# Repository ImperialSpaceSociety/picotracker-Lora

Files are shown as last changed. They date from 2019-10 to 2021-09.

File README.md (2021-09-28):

# Pico Ballon Tracker using LoRaWAN

## Objectives
This Pico balloon tracker is a new version to be designed by Imperial College Space Society. It is intended to offer an easy to build and low cost entry for people who want to launch small Helium filled balloons with a small tracking payload while using the Things Network LoRaWAN Network to receive the telemetry data from the balloon.

 implentation objective is to fly a small balloon around the world and to track it using the Things Network and HabHub.

## Major components
We have settled on the following components to go on the tracker solution. 

### Tracker

* Murata ABZ LoRa Module MCU with 868MHz LoRaWAN Radio and 32 Bit ARM CPU
* Ublox Max M8Q GPS module
* MS8607 Pressure temp humidity sensor
* Solar Power Management
* Possible small Energy storage by battery or super capacitor
The moto: KEEP IT SIMPLE

### TTN2HabHub Bridge

* Subscribe to Things Network Application for data from trackers
* Store Tracker data and meta data showing gateway information
* Forward tracking data to HabHub
* Possibly send data back to tracker
The bridge can be found in a seperate repo: [link](https://github.com/ImperialSpaceSociety/ttnhabbridge)

### Launch Gateway

* Portable Things Network LoRaWAN Gateway
* Cellular Internet Access to Things Network
* GPS
* Local Gateway Status Display
* Local Payload Data display

### Balloon

* Low cost 36 inch super pressure balloon
* Prestressed
* Helium Filled

### Tracker Firmware
All firmware used in the trackers can be found here: https://github.com/ImperialSpaceSociety/LoRaMac-node. Its a fork of the Semtech Loramac-node reference firmware.
Note that the code in the current repo is no longer used and is used for reference only.

# Flights
* ICSPACE15: [Flight report](https://www.union.ic.ac.uk/guilds/icseds/2020/01/long-range-lora-balloon-tracker-launch-from-london/)
* ICSPACE16: [Flight report](https://www.union.ic.ac.uk/guilds/icseds/2020/02/balloon-flights-to-austria-and-slovakia/)
* ICSPACE17: [Flight report](https://www.union.ic.ac.uk/guilds/icseds/2020/02/balloon-flights-to-austria-and-slovakia/)
* ICSPACE18: Was lost after launch
* ICSPACE19: [Flight report](https://www.union.ic.ac.uk/guilds/icseds/2020/03/launch-of-icspace19/)
* ICSPACE20 & 21: [Flight report](https://www.union.ic.ac.uk/guilds/icseds/2020/10/icspace21-flight-to-japan-and-icspace20/)
* ICSPACE22: [Flight report](https://www.union.ic.ac.uk/guilds/icseds/2020/12/first-unconfirmed-circumnavigation-of-the-earth-by-ic-space-society-balloon-icspace22/)
* ICSPACE23: [Flight report](https://www.union.ic.ac.uk/guilds/icseds/2020/12/icspace23-launch/)

Past flight paths may be viewed on the [map](https://charts.mongodb.com/charts-project-0-wlibw/public/dashboards/487e7641-c649-4822-abc5-f70eb2e155c7).

# Design Files
The PCBs are designed with Kicad and the latest designs can be found in the [hardware folder](hardware/Kicad/). We have two designs, the a and the b variant. a variant is a fully solar powered tracker with no power storage. The solar cells are directly wired to VCC and GND to power all components. b variant has a 50mAh lipo on board for power storage. The MPPT IC on board, the SPV1040, extracts maximum current from the cells to charge the battery.

As of 29/12/2020, the latest flight proven design is V1.3a. The b variant has not been flown yet.

The schematic of v1.3a is here:


Assembled tracker:

PCB top layer(v1.3a): 


PCB bottom layer(v1.3a):


# Software
We use the KEIL IDE to program the tracker. KEIL can be downloaded and used free of charge for the STM32L0 series of microcontrollers. You will be able to download Keil from [here](https://www2.keil.com/stmicroelectronics-stm32/mdk). Make sure you activate the licence so that you can compile files greater than 30kb of flash. There is no cost for the licence.

We use the ST link to program the STM32L0 microncontroller. You will likely need the ST-link Driver, which can be downloaded from their website: [link]( https://www.st.com/en/development-tools/stsw-link009.html#get-software)

To get the picotracker firmware, run the following to clone the repo. Useful tip: Ensure the repo is cloned to the root folder e.g. `C:\` because there have been issues with the path lengths of the files getting too long for Windows to handle. The repo has very very long paths, a legacy of the LoRaWAN firmware stack by STMicroelectronics.
```bash
git clone https://github.com/ImperialSpaceSociety/picotracker-Lora.git
```
The software on the latest tracker can be found in the [Software folder](Software). You need to navigate to ``Software/Projects/B-L072Z-LRWAN1/Applications/LoRa/End_Node/MDK-ARM/`` and you can open the KEIL project by clicking ``Lora.uvprojx``

Once you open Keil, it should look like this. Ensure that the 1.3a_variant of the code is selected(highlighted in picture): 

You will have to tell Keil that you are using the ST-link programmer. To do that, go to the `flash` drop down menu and select `Configure Flash Tools`. Then switch to the `debug` tab and ensure the drop down menu is set to `St-Link Debugger` as shown in the picture below. Then click the `settings` button.


When you open up the settings menu, it should look like this: 


Now that your st-link debugger is setup, its time to compile and program. Ensure the ST-link programmer is connected to the tracker, and hit compile and then upload or debug. Note: Its necessary to compile before uploading, or it will not have the latest hex file to flash to the tracker.


# Software overview
The picotracker state machine is as follows: 
It gets a GPS fix every 2 minutes and transmits it to ground



### Edits done over the reference version by STMicroelectronics
* Switching LoRaMAC regional settings depending on where it is
* Reduce tx power over US915/AU915
* Prevent sending empty frame after boot
* Use subband of 8 channels for US915/AU915
* Seperate credentials for each region of the world. 
* Prevent sticky uplinks after receiving channel change requests. Actually prevent any uplinks to test channel change requests. Wait till the next scheduled uplink.
* Different datarate for each region
* Polling specific date ranges for eeprom records
* 
# Photos
These are photos of ICSPACE19 before launch, during testing in the sun. It is a 1.1a variant, with no power storage.

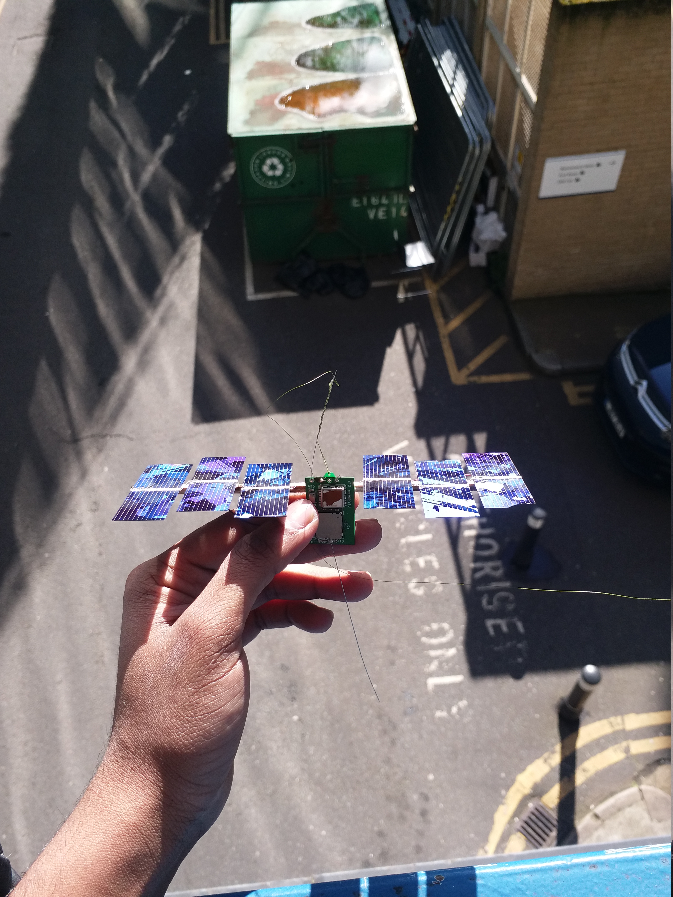
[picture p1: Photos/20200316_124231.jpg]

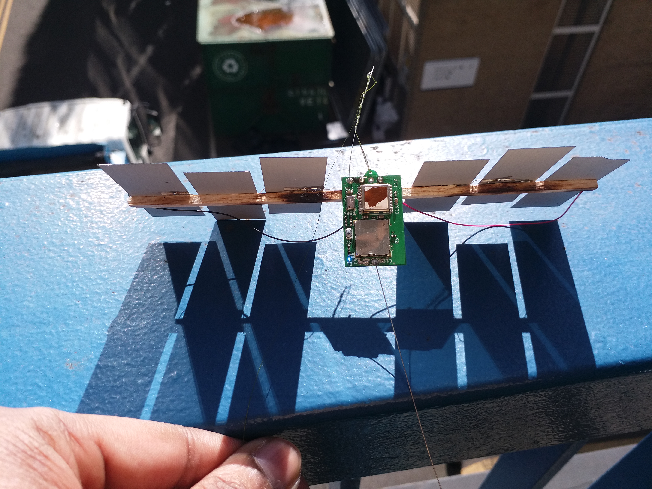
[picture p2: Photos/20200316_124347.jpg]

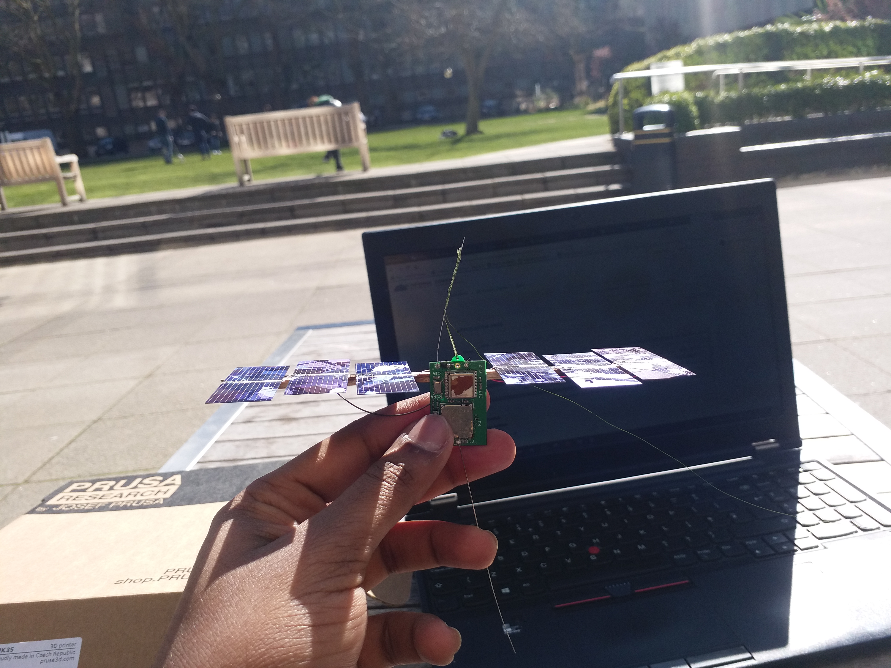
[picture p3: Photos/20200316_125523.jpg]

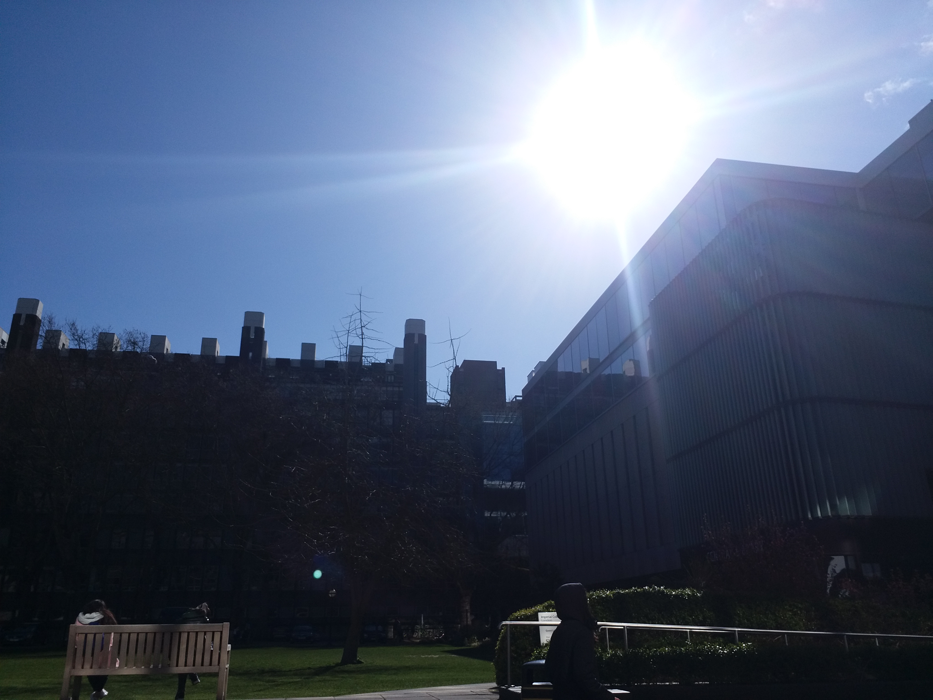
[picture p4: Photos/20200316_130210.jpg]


# Instructions for special tests of multiregion Lorawan

In this test, I want to test if the tracker will work properly over US915. We have had issues where some packets over Canada contained no payload data. I don't know the root cause. Could be power supply issues. To narrow down causes, I have created this test, to be run on the B-L072Z-LRWAN1.

This test will:
1. transmit every 2 minutes
2. a packet the size of our typical message
3. on US915 frequencies.

I want to find out if we receive any empty packets.

## How to run the program

Clone this project and switch to branch `multi-region-tests`. All tests on multi region lorawan will be here.
Navigate to `picotracker-Lora/Software/Projects/B-L072Z-LRWAN1/Applications/LoRa/End_Node/MDK-ARM/` and run `Lora.uvprojx` with Keil.

After opening the Keil project, switch the firmware config to work on the B-L072Z-LRWAN1 dev board. This can be done as follows: 

Now compile and upload the code into the dev board.

The board will output debug information at `20000000` baud. I normally use the Arduino editor's inbuilt terminal. 

An expected output on the terminal will look like this. It will initialise, and transmit a packet every 2 minutes. This packet will be the same size as the ones transmitted over Canada on ICSPACE22 and will be transmitting on US915 freqencies. This will replicate the same parameters of ICSPACE22 over Canada, where we saw that some packets did not contain any data at all. Note that this program will not need any peripherals(GPS, sensors etc).
```

************************************ 
* Picotracker Lora                 * 
* Imperial College Space Society   * 
************************************ 

SELFTEST: Initialising Hardware
SELFTEST: LED should blink now
SELFTEST: Now initing sensors
SELFTEST: Initialisng ms5607
SELFTEST: Now the radio should transmit
APP DUTY CYCLE(TX INTERVAL maybe longer depending on message length and datarate) : 12000
ABP
DevEui= 00-AB-DF-8A-62-F5-C1-81
DevAdd=  26011673
NwkSKey= D1 21 88 24 49 F6 0C 62 C0 C1 EF 4E FC 24 EC E4
AppSKey= 8F 3C F3 ED 51 FE 03 64 EC 0E 1A 06 6D 41 FC 9D

READING SENSOR AND GPS
================================================================
SENSOR AND GPS VALUES
================================================================
Temperature degrees C: 0.000000
Pressure mBar: 0.000000
Longitude: 0.000000 Latitude: 0.000000 altitude: 0
Solar voltage no load: 3
Solar voltage with GPS load: 0
================================================================
TX on freq 904600000 Hz at DR 4
⸮  1s615ms: PHY txDone
⸮RX on freq 923900000 Hz at DR 13
⸮  2s646ms: PHY rxTimeOut
⸮RX on freq 923300000 Hz at DR 8
⸮  3s698ms: PHY rxTimeOut
  3s707ms: APP> McpsConfirm STATUS: OK

  3s707ms: #= U/L FRAME 6640 =# Class A, Port 99, data size 26, pwr 2, Channel Mask FF00 

⸮READING SENSOR AND GPS

================================================================
SENSOR AND GPS VALUES
================================================================
Temperature degrees C: 0.000000
Pressure mBar: 0.000000
Longitude: 0.000000 Latitude: 0.000000 altitude: 0
Solar voltage no load: 3
Solar voltage with GPS load: 0
================================================================
TX on freq 904600000 Hz at DR 4
⸮ 13s642ms: PHY txDone
⸮RX on freq 923900000 Hz at DR 13
⸮ 14s673ms: PHY rxTimeOut
⸮RX on freq 923300000 Hz at DR 8
⸮ 15s726ms: PHY rxTimeOut
 15s735ms: APP> McpsConfirm STATUS: OK

 15s735ms: #= U/L FRAME 6641 =# Class A, Port 99, data size 26, pwr 2, Channel Mask FF00 
```
### Speed up debugging tips
If you want to speed up the process for debugging, in `main.h`, you can set `APP_TX_DUTYCYCLE` to a lower value to increase the frequency of transmissions.
```c
#define APP_TX_DUTYCYCLE                           120000
```

For debugging, you can switch the end node to transmit on EU868 frequencies by making the following changes to `geofence.c`
```c
LoRaMacRegion_t current_loramac_region = LORAMAC_REGION_EU868;  // Loramac region EU868
Polygon_t curr_poly_region = EU863870_EUROPE_polygon; // Europe is in this polygon
```

### Verify the data(the actual test)
Now if everything is working on the end node side, it is time to see what is appearing on the TTN console. 
You should be able to see packets of data that look something like this. The important thing is, in order to pass this test, every packet should have a `payload_raw` and `payload_fields` section. During ICSPACE22's flight over Canada, we found that some packets did not contain the `payload_fields` section. I want to find out if it is a software issue that causes it.

Note, that every single piece of MQTT data is archived [here](http://medadnewman.co.uk/wp-content/uploads/2020/10/mqtt_log_data-1.txt) for reference. 
```json
{
  "app_id": "icss_lora_tracker",
  "dev_id": "icspace23",
  "hardware_serial": "0093BECA9134091B",
  "port": 99,
  "counter": 6603,
  "payload_raw": "AHN2YwFnERICiAAAAAAAAAAAAAMCAAAEAQA=",
  "payload_fields": {
    "analog_in_3": 0,
    "barometric_pressure_0": 3030.7,
    "digital_out_4": 0,
    "gps_2": {
      "altitude": 0,
      "latitude": 0,
      "longitude": 0
    },
    "temperature_1": 437
  },
  "metadata": {
    "time": "2020-11-06T22:20:03.034197954Z",
    "frequency": 868.5,
    "modulation": "LORA",
    "data_rate": "SF8BW125",
    "airtime": 154112000,
    "coding_rate": "4/5",
    "gateways": [
      {
        "gtw_id": "eui-58a0cbfffe800f4d",
        "timestamp": 3440028508,
        "time": "2020-11-06T22:20:03.082736968Z",
        "channel": 0,
        "rssi": -67,
        "snr": 8.5,
        "rf_chain": 0
      }
    ]
  }
}

```

## License

Hardware is Licensed under CERN OHL v.1.2 or later https://www.ohwr.org/documents/294 No warranty is provided for this documentation implied or otherwise.

Software is licensed under MIT License.

MIT License

Copyright (c) 2018 Imperial College Space Society

Derived Software  Copyright (c) 2014  Richard Meadows <richardeoin>

Permission is hereby granted, free of charge, to any person obtaining a copy of this software and associated documentation files (the "Software"), to deal in the Software without restriction, including without limitation the rights to use, copy, modify, merge, publish, distribute, sublicense, and/or sell copies of the Software, and to permit persons to whom the Software is furnished to do so, subject to the following conditions:

The above copyright notice and this permission notice shall be included in all copies or substantial portions of the Software.

THE SOFTWARE IS PROVIDED "AS IS", WITHOUT WARRANTY OF ANY KIND, EXPRESS OR IMPLIED, INCLUDING BUT NOT LIMITED TO THE WARRANTIES OF MERCHANTABILITY, FITNESS FOR A PARTICULAR PURPOSE AND NONINFRINGEMENT. IN NO EVENT SHALL THE AUTHORS OR COPYRIGHT HOLDERS BE LIABLE FOR ANY CLAIM, DAMAGES OR OTHER LIABILITY, WHETHER IN AN ACTION OF CONTRACT, TORT OR OTHERWISE, ARISING FROM, OUT OF OR IN CONNECTION WITH THE SOFTWARE OR THE USE OR OTHER DEALINGS IN THE SOFTWARE.

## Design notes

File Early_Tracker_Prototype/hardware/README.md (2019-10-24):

## TODO
* set up circuit to measure solar voltage
* verify if gps circuit is correct
* layout the PCB

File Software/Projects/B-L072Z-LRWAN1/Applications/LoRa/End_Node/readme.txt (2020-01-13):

/**
  @page End_Node Readme file
 
  @verbatim
  ******************************************************************************
  * @file    End_Node/readme.txt 
  * @author  MCD Application Team
  * @brief   This application is a simple demo of a LoRa Object connecting to 
  *          a LoRa Network. 
  ******************************************************************************
  *
  * Copyright (c) 2018 STMicroelectronics. All rights reserved.
  *
  * This software component is licensed by ST under Ultimate Liberty license
  * SLA0044, the "License"; You may not use this file except in compliance with
  * the License. You may obtain a copy of the License at:
  *                               www.st.com/SLA0044
  *
  ******************************************************************************
   @endverbatim

@par Example Description

This directory contains a set of source files that implements a simple demo of an end 
device also known as a LoRa Object connecting to a Lora Network. The LoRa Object can be 
   - either a STM32LXxx-Nucleo board and Lora Radio expansion board, optionnally a sensor board. 
   - or a B-L072Z-LRWAN1 (available soon)
By setting the LoRa Ids in comissioning.h file according to the LoRa Network requirements, 
the end device will send periodically the sensor data to the LoRa network.
  ******************************************************************************

@par Directory contents 

  - End_Node/LoRaWAN/App/inc/bsp.h               Header for bsp.c
  - End_Node/LoRaWAN/App/inc/Commissioning.h     End device commissioning parameters
  - End_Node/LoRaWAN/App/inc/debug.h             interface to debug functionally
  - End_Node/LoRaWAN/App/inc/hw.h                group all hw interface
  - End_Node/LoRaWAN/App/inc/hw_conf.h           file to manage Cube SW family used and debug switch
  - End_Node/LoRaWAN/App/inc/hw_gpio.h           Header for hw_gpio.c
  - End_Node/LoRaWAN/App/inc/hw_msp.h               Header for driver hw msp module
  - End_Node/LoRaWAN/App/inc/hw_rtc.h            Header for hw_rtc.c
  - End_Node/LoRaWAN/App/inc/hw_spi.h            Header for hw_spi.c
  - End_Node/LoRaWAN/App/inc/utilities_conf.h    configuration for utilities
  - End_Node/LoRaWAN/App/inc/vcom.h              interface to vcom.c
  - End_Node/LoRaWAN/App/inc/version.h           version file
  - End_Node/Core/inc/stm32lXxx_hal_conf.h       Library Configuration file
  - End_Node/Core/inc/stm32lXxx_hw_conf.h        Header for stm32lXxx_hw_conf.c
  - End_Node/Core/inc/stm32lXxx_it.h             Header for stm32lXxx_it.c
  
  - End_Node/LoRaWAN/App/src/bsp.c               manages the sensors on the application
  - End_Node/LoRaWAN/App/src/debug.c             debug driver
  - End_Node/LoRaWAN/App/src/hw_gpio.c           gpio driver
  - End_Node/LoRaWAN/App/src/hw_rtc.c            rtc driver
  - End_Node/LoRaWAN/App/src/hw_spi.c            spi driver
  - End_Node/LoRaWAN/App/src/main.c              Main program file
  - End_Node/LoRaWAN/App/src/vcom.c              virtual com port interface on Terminal
  - End_Node/Core/src/stm32lXxx_hal_msp.c        stm32lXxx specific hardware HAL code
  - End_Node/Core/src/stm32lXxx_hw.c             stm32lXxx specific hardware driver code
  - End_Node/Core/src/stm32lXxx_it.c             stm32lXxx Interrupt handlers
 
@par Hardware and Software environment 

  - This example runs on STM32L053R8, STM32L073RZ, STM32L152RE and STM32L476RG devices.
    
  - This application has been tested with STMicroelectronics:
    NUCLEO-L053R8 RevC
    NUCLEO-L073RZ RevC
    NUCLEO-L152RE RevC
    NUCLEO-L476RG RevC	
    B-L072Z-LRWAN1 RevC
    boards and can be easily tailored to any other supported device 
    and development board.

  - STM32LXxx-Nucleo Set-up    
    - Connect the Nucleo board to your PC with a USB cable type A to mini-B 
      to ST-LINK connector (CN1 / CN7 on B-L072Z-LRWAN1).
    - Please ensure that the ST-LINK connector CN2 (CN8 on B-L072Z-LRWAN1) jumpers are fitted.
  -Set Up:

             --------------------------  V    V  --------------------------
             |      LoRa Object       |  |    |  |      LoRa Netork       |
             |                        |  |    |  |                        |
   ComPort<--|                        |--|    |--|                        |-->Web Server
             |                        |          |                        |
             --------------------------          --------------------------

@par How to use it ? 
In order to make the program work, you must do the following :
  - Open your preferred toolchain 
  - Rebuild all files and load your image into target memory
  - Run the example
  - Open two Terminals, each connected the respective LoRa Object
  - Terminal Config = 115200, 8b, 1 stopbit, no parity, no flow control ( in src/vcom.c)
   
 * <h3><center>&copy; COPYRIGHT STMicroelectronics</center></h3>
 */

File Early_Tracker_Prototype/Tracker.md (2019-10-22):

# Tracker Prototype

It was decided to prototype key features of the new tracker on develop board before starting detail of hardware and firmware design.

### Tracker

* Murata ABZ LoRa Module MCU with 868MHz LoRaWAN Radio and 32 Bit ARM CPU
* Ublox Max M8Q GPS module
* MS8607 Pressure temp humidity sensor
* Solar Power Management
* Peripheral Power Control to minimise power consumption
* Possible small Energy storage by battery or super capacitor
* Reset Manager to ensure no corruption in case of brown outs
The moto: KEEP IT SIMPLE

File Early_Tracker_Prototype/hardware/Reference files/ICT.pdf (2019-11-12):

## ICT-series WSPR balloon tracker capable of WSPR and JT9

Rev. 1, September 2019

## Instructions

Original based on HABalloon by Stephen KD2NDR, Miami, Florida, October 25 2018

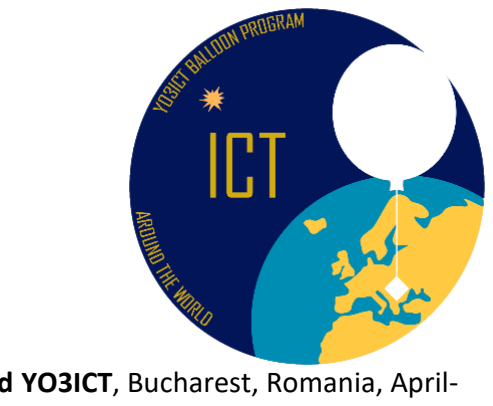
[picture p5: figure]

Improvements, advanced telemetry, new features, ground testing and flight testing by Eduard YO3ICT, Bucharest, Romania, April-September 2019

Credits also go to Hans G0ULP for developing the telemetry protocol and to David VE3KCL, Mike SA6BSS and Ben PE2BZ for all the help received during testing and flying.

You may use and modify the following code to suit your needs so long as it remains open source and it is for non-commercial use only.

The following software and hardware flew on ICT1, ICT2 and ICT3 balloons in 2019.

In the provided archive you will find the source code and the PCB layout files. This document is provided as a tutorial to get you up and running.
Fly at your own risk and follow your local aviation laws.

## Contact:

## Firmware instructions

All of the following assume that you are using the usbasp AVR programmer.

Before going into the firmware itself, our little board’s AVR chip runs at 4MHz. We need to set up some fuse bits using avrdude command lines.

We need to set the AVR to run on the external 4MHz resonator and the BOD level at 1.8V (Low fuse FD, High fuse DA, Extended fuse 06).

Avrdude commands:

avrdude -c usbasp -p m328p -v -U lfuse:w:0xFD:m

avrdude -c usbasp -p m328p -v -U hfuse:w:0xDA:m

avrdude -c usbasp -p m328p -v -U efuse:w:0x06:m

Install the latest Arduino IDE.

Then we set up our little board with the correct initialization.

Copy the code from the included boards.txt file to the end of your boards.txt file found under Program Files/arduino/hardware/arduino/avr and then choose this board in the Tools menu.

Next, we are using the delayMicroseconds function. We need to get the Arduino IDE aware of our 4Mhz clock. You'll need to replace the wiring.c file under Program Files/arduino/hardware/arduino/avr/cores/arduino. Replace the existing file with the one found in the archive.

Libraries required:

1. Time library : https://github.com/PaulStoffregen/Time
2. GPS library https://github.com/mikalhart/TinyGPSPlus
3. Si5351 library https://github.com/etherkit/Si5351Arduino
4. JT Encode library https://github.com/etherkit/JTEncode

Download all of them and install them in your libraries directory. You can also use Sketch – Include library menu from the Arduino IDE. Just point it to the zip file of each library and they will be installed quickly.

Edit the files to fit your conditions.

Important settings to do:

1. Callsign is set in the main .ino file on line 31. The provided source code comes with the fake callsign AA0AAA
2. Actual Si5351 oscillator frequency is set on line 242 of TelemFunctions.h. The provided source code comes with 27000000, meaning 27MHz
3. In ModeDef.h lines 11 and 12 we define the actual on-air frequencies for JT9 and WSPR
4. The telemetry channel is set in TelemFunctions.h on lines 80 and 81. Basically, we hard-code the first and the third characters of the telemetry callsign.

Please read this: http://www.qrp-labs.com/ultimate3/ve3kcl-balloons/ve3kcl-s4.html#protocol to get a better understanding of the telemetry protocol and channels.

Please read this: http://hojoham.blogspot.com/2016/10/known-flight-ids.html for known flight IDs. Ask Mike KD2EAT to get your channel assigned. Note: The list might change, as it contains some invalid channels (the ones starting with “1”).

The provided source code comes with an invalid telemetry channel to avoid interference while testing.

5. In TelemFunctions.h there are a lot of math functions (function loc_dbm_telem), including the temperature and solar voltage conversion formulas. Please calibrate them. Each AVR device may give different results. I provide a sample sketch (TEMP_VOLT_TEST). The PCB has a pad named TX. Hook up your UART to USB dongle to get the data out.
6. The source code provided has build-in three timing files for different timings of the WSPR and/or JT9 modes. The file can be selected within the main .ino file on line 61. You can include a different file. The only flight proven timing file is timing3.h. You can also domake your own file. Just test. And test again. And test once more before flight.

The timing3.h file uses both JT9 and WSPR. The transmission schedule is based on a 6 minute transmission cycle:

Minute 2 - JT9 - Callsign + 6-digit locator
Minute 3 - JT9 - 7th and 8th of the extended 8-digit locator + Altitude + Ground speed
Minute 4 - WSPR - Standard WSPR message
Minute 6 - WSPR - WSPR telemetry

Minute 12 - WSPR - Standard WSPR message
Minute 14 - WSPR - WSPR telemetry Minute 16 - WSPR - Standard WSPR message

Minute 22 - WSPR - Standard WSPR message Minute 24 - WSPR - WSPR telemetry Minute 26 - WSPR - Standard WSPR message

Minute 32 - JT9 - Callsign + 6-digit locator
Minute 33 - JT9 - 7th and 8th of the extended 8-digit locator + Altitude + Ground speed Minute 34 - WSPR - Standard WSPR message
Minute 36 - WSPR - WSPR telemetry

Minute 42 - WSPR - Standard WSPR message
Minute 44 - WSPR - WSPR telemetry Minute 46 - WSPR - Standard WSPR message

Minute 52 - WSPR - Standard WSPR message Minute 54 - WSPR - WSPR telemetry Minute 56 - WSPR - Standard WSPR message

Known bugs

Solar voltage is reported incorrectly. The hardware resistor divider R4 & R6 values should be changed to allow for greater voltage swing. The voltage formula must be recalculated as well.

## Hardware instructions

The PCB files provided are flight proven. Use a 50ohm resistor dummy load for testing. The PCB is 0.6mm thick.

Solder all the components. Note: The tracker won’t start without the GPS module.

The GPS antenna is made of 4.5cm of guitar string wire. It has a dedicated mounting hole.

The solar panels (6 pieces, the 39x19mm size) are soldered together in series using guitar string wire.

Pictures for reference:

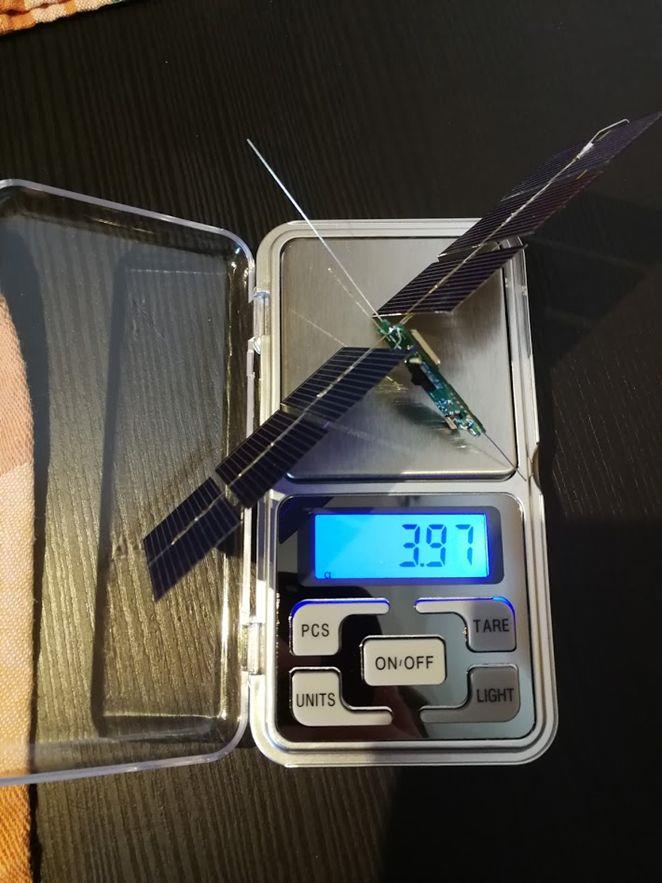
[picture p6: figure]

Three panels on each side.

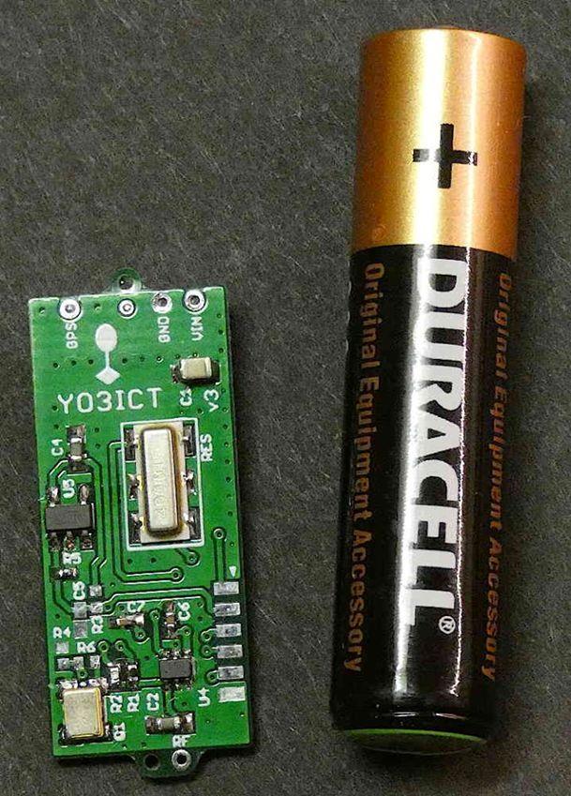
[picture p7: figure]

There are some holes on the PCB for power (which comes also via guitar string wire) and an isolated tinned hole near the top, just below the top tether hole.

That isolated tinned hole is for suspending the solar cells. The guitar string wire segment that connects the 3rd to the 4th solar cell is passing through that hole and is soldered. This provides stiffness as well as flexibility in the solar panel system. This is essential to ensure trouble-free mounting, handling, launching and flying.

The antenna is made of thin 0.1mm copper wire suspended by 0.08mm dynemaa fishing string. The string attaches to the two dummy holes at top and bottom of the PCB. The ’hot’ part of the dipole attaches to the dedicated hole named RF at the bottom. The ’cold’ part of the dipole gets attached to GND AFTER the solar panels have been attached. Try to provide some slack to the thin copper antenna wire before soldering. Failing to do so might result in broken solar cells or antenna wires.

Solar cells need to be soldered quickly and cleanly. Use flux, pre-solder the guitar string wire and use a temperature controller soldering iron (~330 degrees Celsius). Also, solar panels should be as horizontal as possible, otherwise the startup sun angle will be unpredictable.

The programming port pads are located on the side of the PCB and the white arrow points to the positive pad. The connector needed is a 1.27mm pitch row connector. This is to be removed before flight to save weight. Also clean the pads to get rid of excess solder. The programming layout is custom due to the PCB limitations.

In the end, the PCB is coated with some lacquer and then it is covered with kapton tape. This increases the thermal mass a bit, avoids moisture on the PCB and also helps with some basic thermal insulation.

The tracker and solar cells must came close to 4 grams weight and the antenna (whole dipole for 14MHz) should weigh less than one gram.

## What balloon to use?

SBS balloon or Chinese clear balloons, found on Aliexpress? As the SBS balloons are very expensive, we’ll discuss the cheap ones.

Order as many as you can afford. Usually, the ones from the center of the packaging are damage-free.

The balloons need to be pressure tested and pre-stretched to allow for greater internal volume and higher altitude. Your best shot at circumnavigation is to fly above 11000m, at least.

Required:

1. Air mattress pump for rapid inflation/deflation
2. Aquarium pump for controlled presurization
3. Digital, differential manometer

Basically, the pre-stretch process is a matter of time, pressure and temperature.

To shed weight, cut the excess material around the balloon edge and also cut the top tether, unless you do a dual launch. Do this BEFORE any attempt at balloon presurization.

Target differential pressure is above 0.6 psi. Go slowly above 0.4 psi. This will also highlight defective balloons. Use the hair dryer on moderate position to heat the balloon as you increase the pressure.

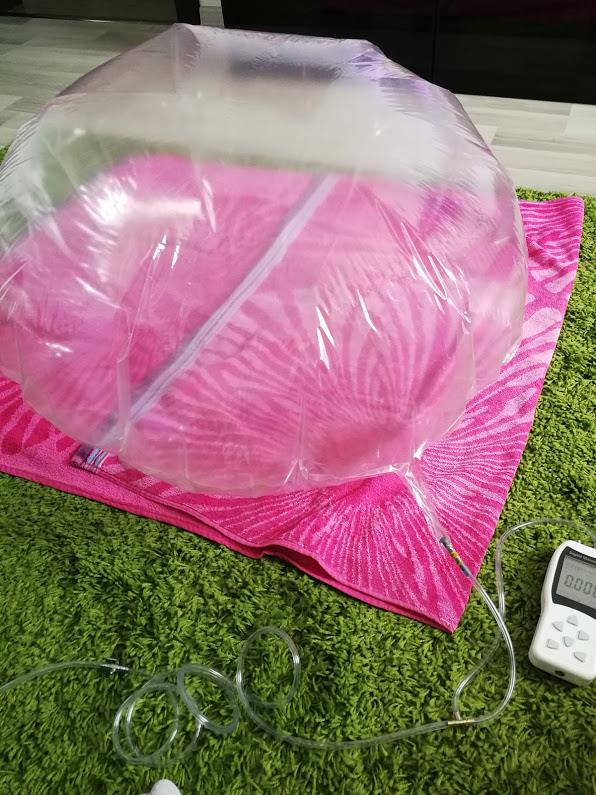
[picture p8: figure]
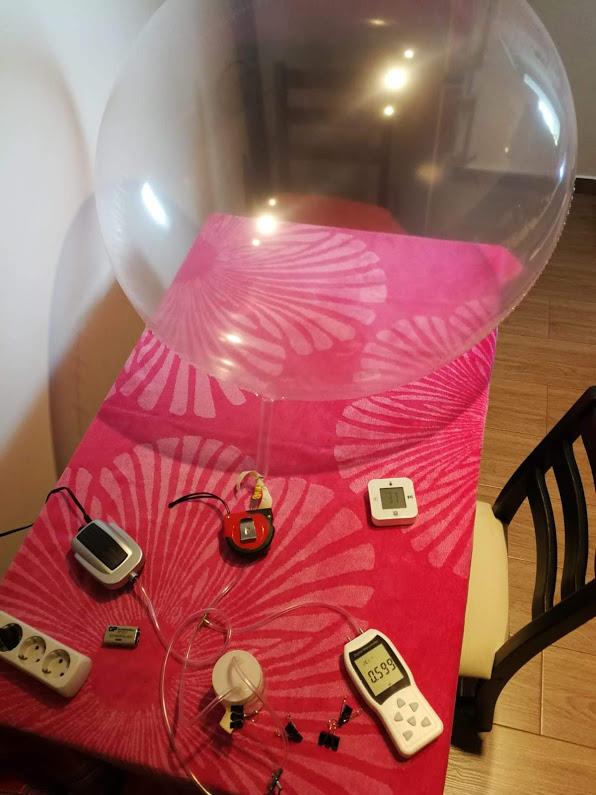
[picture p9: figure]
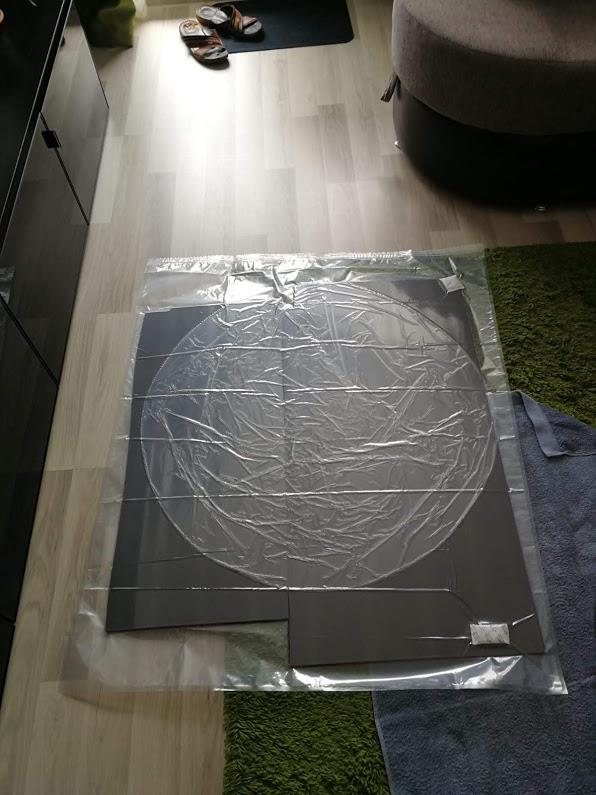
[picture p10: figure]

The target should be a pressure of around 0.6-0.65 psi, no balloon wrinkles on the edge and let it sit overnight. You will want to experiment as different balloons and different pressures and temperatures means different results. Not all balloons are created equal. David VE3KCL and Mike SA6BSS have a lot of experience with this type of balloon.

After the overnight pressurization, it is time to put the balloon to storage, in preparation for launch. Use a clothes vacuum bag and some dessicant bags. Avoid excess stress on the balloon!

## Launch

Use H2 for the best performance and highest altitude.

If using He, use the purest available, some retailers only offer 80% this will result in reduced performance and altitude.

1. Lay out a sheet to unfold the balloon on. Handle the balloon with care, try not to wrinkle the film any more than you have to. Avoid wearing clothes with zippers or buttons that may come in contact with the balloon.
2. Filling and launching a super pressure balloon requires a very special skill set. The most important is filling the balloon so it has the correct free lift. Please fill indoors and turn off heating and air conditioning, so the room is very still. Weigh everything that will be attached to the balloon, tracker, load line, tape, etc. Then add a maximum of 8 grams of free lift. I recommend you practice these procedures with a party balloon to refine your skills because if you over fill the balloon it will burst.
3. Once the fill is done, it’s time to seal the neck.
4. Set the iron to around 140 degrees Celsius. You can experiment with different temperatures here.
5. You need a hard surface like wood to put a piece of a mouse pad on. Make sure there are no sharp edges. Lay the balloon neck down on the mouse pad.
6. Use a piece of parchment paper. Cut a piece of it to lay on top of the neck so the iron does not come in direct contact with the film.
7. Press the edge of the iron down FIRMLY on top of the parchment paper and hold iron in place for 3 to 5 seconds.
8. Iron the rest of the neck.
9. Attach payload to the neck of the balloon. You can trim the neck at this point.
10. Time to launch – good luck! Avoid launching in the winter. Low sun angle means that the daily run time of the tracker will be very low. Avoid launching in high winds. Avoid launching near airports.

Sealed neck pictures:

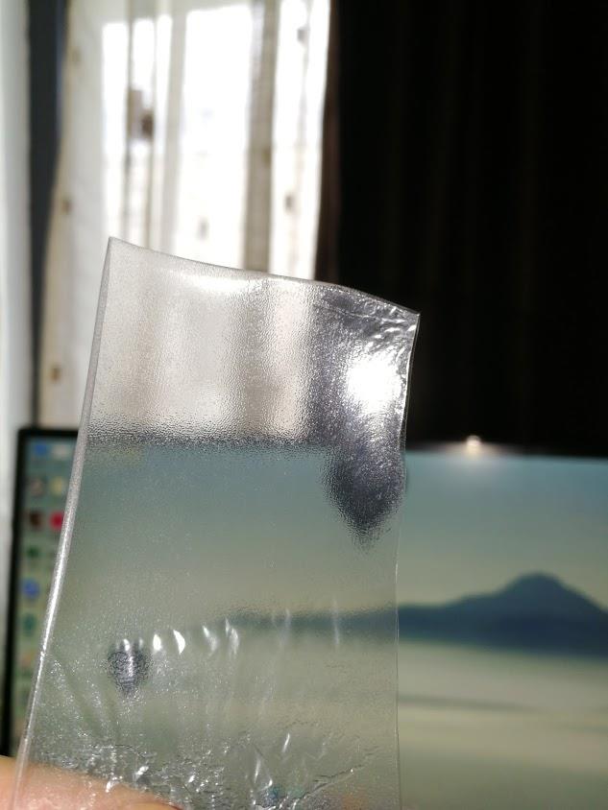
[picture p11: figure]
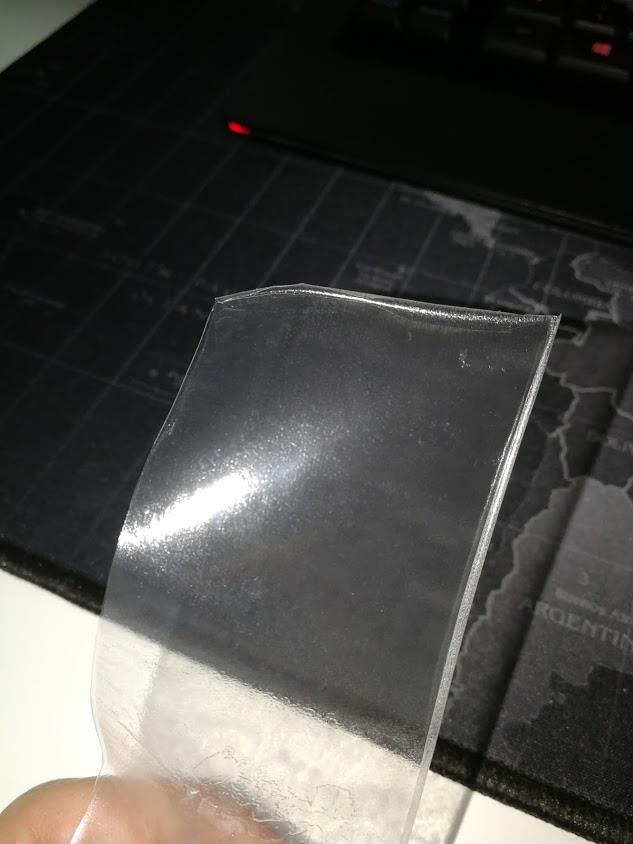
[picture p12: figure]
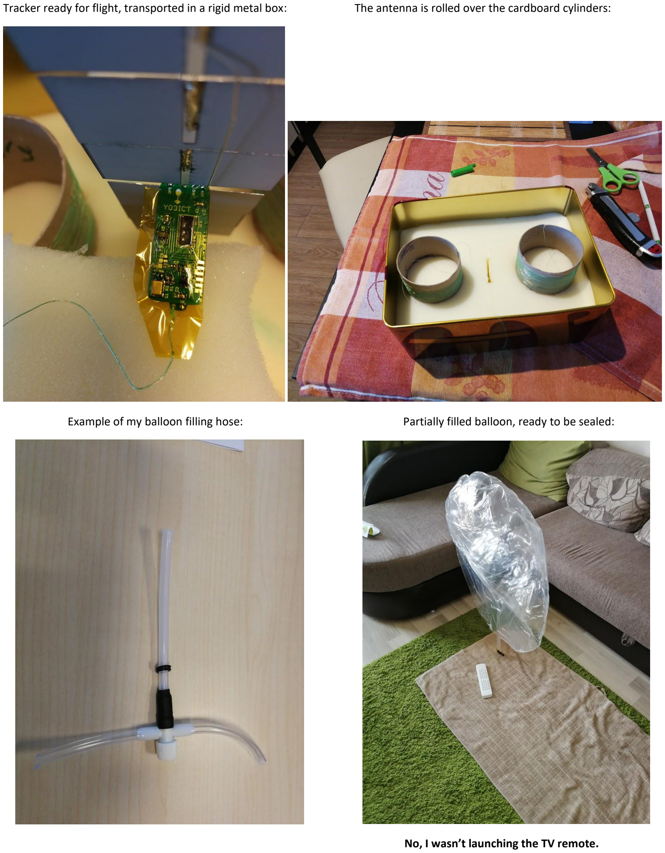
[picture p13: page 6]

Tracker ready for flight, transported in a rigid metal box: | The antenna is rolled over the cardboard cylinders:
Example of my balloon filling hose: | Partially filled balloon, ready to be sealed:

No, I wasn’t launching the TV remote.

ICT1 launch. You can clearly see the top and bottom antenna legs with the tracker in the middle:

## Tracking

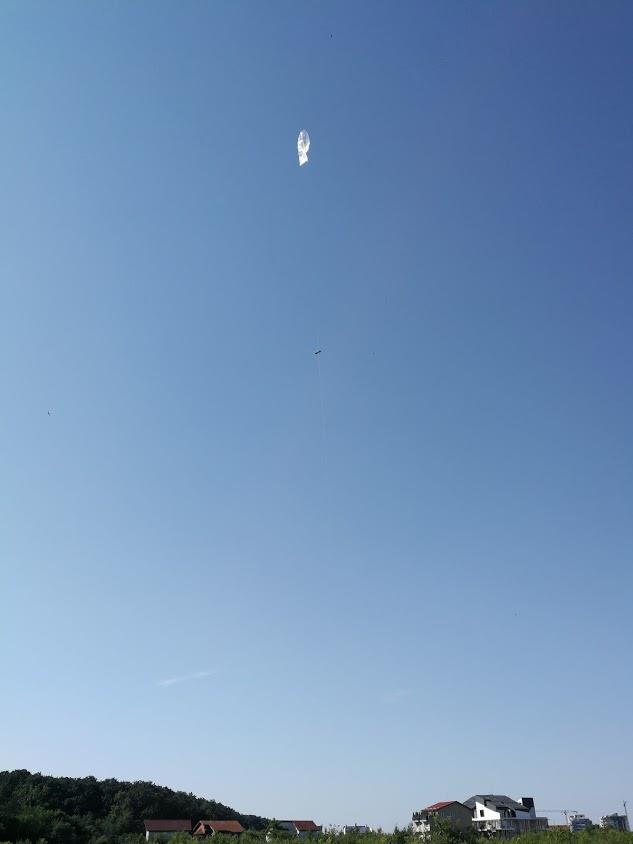
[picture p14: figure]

To get your balloon tracker on the tracker.habhub.org page please send email to David SM3ULC. You can also keep your own tracking map by programming a Phyton script or some VB code inside an Excel file. Contact me if you need help.

The WSPR network is big, but there’s an area with very low coverage : East-Central Asia. You’ll need to help your balloon by using some of the available KiwiSDRs (sdr.hu) from that area.

The best KiwiSDRs are Novosibirsk and Khabarovsk (Russia), Fukushima (Japan), Hawaii and KPH (California). Not all of them are always online. Do not rely on the build-in WSPR decoder. Feed the audio to a local instance of WSJT-X.

## Good luck and clear skies!

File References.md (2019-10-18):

# Links to Useful Documents

## SAM L21
[Datasheet and Reference manual](https://www.farnell.com/datasheets/2014285.pdf)

[Atmel� Software Framework (ASF) Reference Manual](http://ww1.microchip.com/downloads/en/AppNotes/Atmel-42699-ASF-Manual-(SAML21)_ApplicationNote_AT11513.pdf)

[Getting started guidelines](http://ww1.microchip.com/downloads/en/AppNotes/atmel-42410-getting-started-with-saml21_application%20note_at03975.pdf)

[SAM L21 Xplained Pro manual](http://ww1.microchip.com/downloads/en/devicedoc/atmel-42405-saml21-xplained-pro_user-guide.pdf)

## Si4468
[Datasheet](https://www.silabs.com/documents/public/data-sheets/Si4464-63-61-60.pdf)

[Programming Guide](https://www.silabs.com/documents/public/application-notes/AN633.pdf)

[API Documentation](http://www.silabs.com/documents/public/application-notes/EZRadioPRO_REVB1_API.zip)

## Bristol SEDS

[Main Page](http://www.bristol-seds.co.uk/)

[PicoTracker GitHub](https://github.com/bristol-seds/pico-tracker)

## HAB

[UKHAS Google Group](https://groups.google.com/forum/#!forum/ukhas%5B261-280%5D)

## uBlox

[BN-220](https://surehobby.com/desc/HR/HR5512/BN_220_GPS_Antenna_datasheet.pdf)

[UBX-M8030 Specification](https://www.u-blox.com/sites/default/files/products/documents/UBX-M8030-KT-FT_ProductSummary_%28UBX-14001605%29.pdf)

[Protocol Specification](https://www.u-blox.com/sites/default/files/products/documents/u-blox8-M8_ReceiverDescrProtSpec_%28UBX-13003221%29_Public.pdf)

## BME280

[BME280 Data Sheet](https://www.embeddedadventures.com/datasheets/BME280.pdf)

[Official Bosch C Driver](https://github.com/BoschSensortec/BME280_driver)

[Larry Banks C library](https://github.com/bitbank2/bme280)

## RFM98W

[Datasheet](http://www.farnell.com/datasheets/1870822.pdf)

[SX127x Datasheet](https://cdn-shop.adafruit.com/product-files/3179/sx1276_77_78_79.pdf)

[C Code example](https://github.com/wdomski/SX1278-example)

## UKHAS Lora

[Tracking Guide](https://ukhas.org.uk/guides:lora_tracking_guide)

## Stuart Robinsons Tracker

[Lora Tracker](http://www.loratracker.uk/?p=30)

[Github](https://github.com/LoRaTracker)

## TomasTT7 Trackers

[TT7B Tracker Blog](http://tt7hab.blogspot.com/2018/09/the-tt7b-tracker.html)

[tt7B Github](https://github.com/TomasTT7/TT7B-Tracker)

## Pi in the Sky

[Lora Tracker](http://www.pi-in-the-sky.com/index.php?id=making-a-lora-tracker)

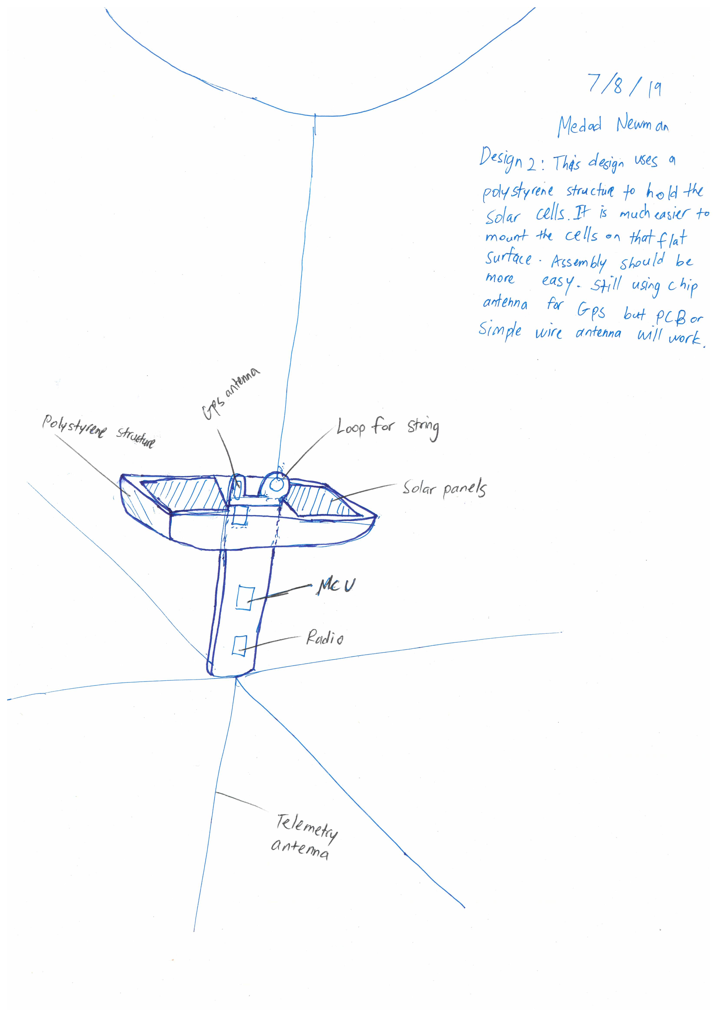
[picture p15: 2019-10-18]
Early_Tracker_Prototype/hardware/Plans/Design 2.jpg

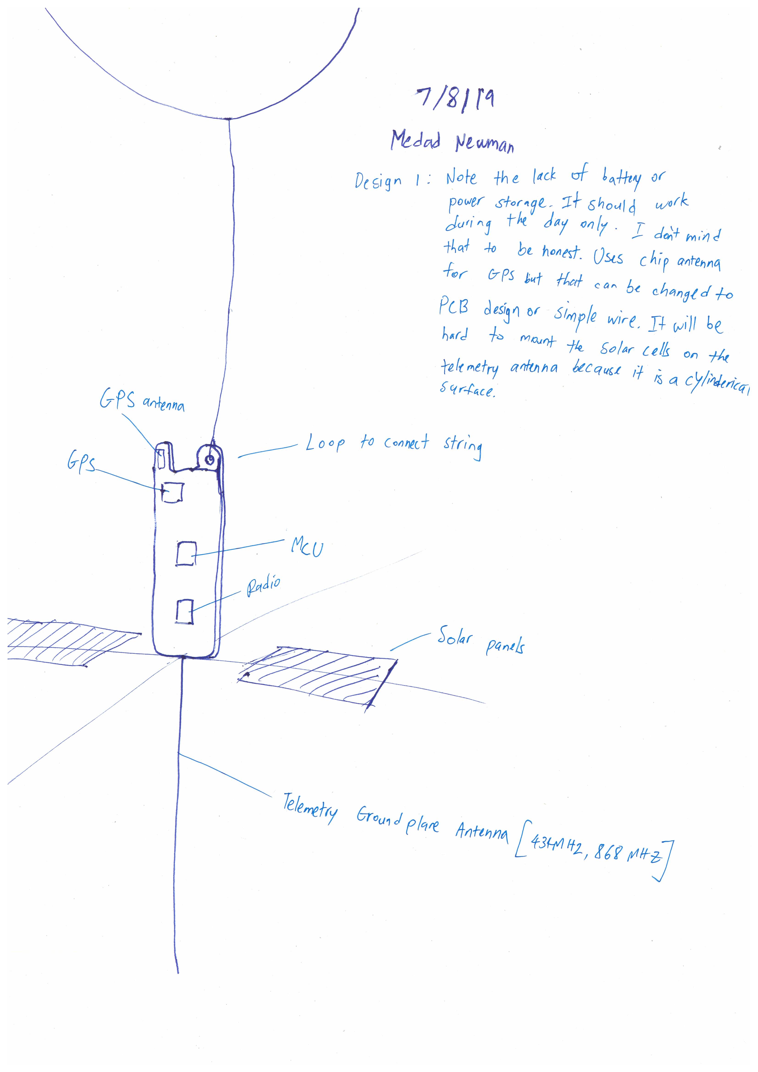
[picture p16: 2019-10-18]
Early_Tracker_Prototype/hardware/Plans/Design 1.jpg

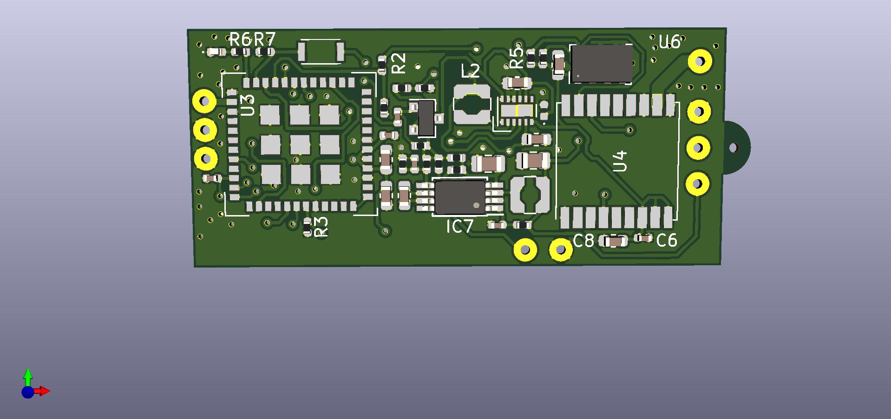
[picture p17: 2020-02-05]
hardware/Kicad/Picotracker V1.2b/circuit board design.jpg

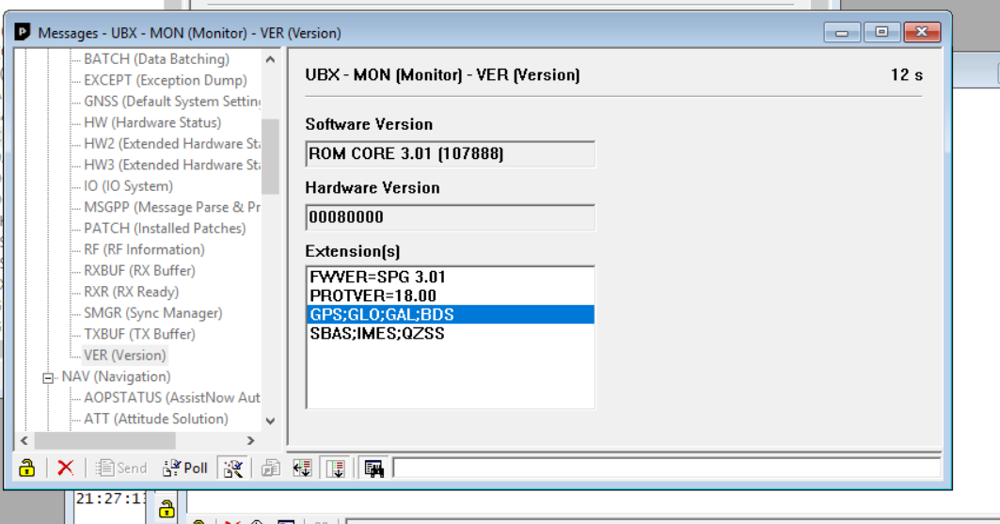
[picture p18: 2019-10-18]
Early_Tracker_Prototype/hardware/GPS information/version information.PNG

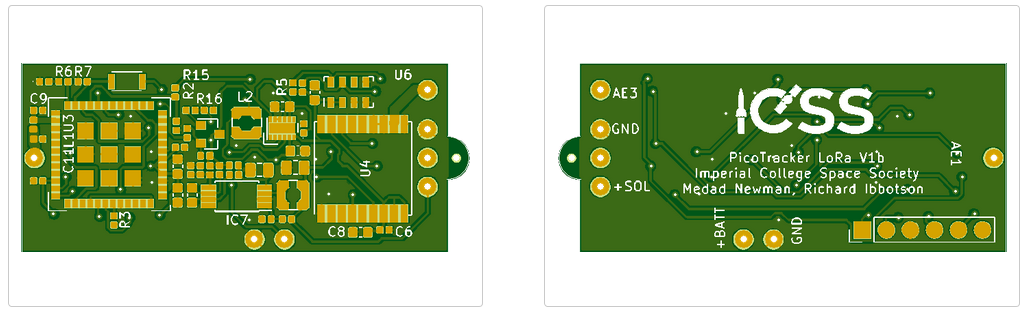
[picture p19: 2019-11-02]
hardware/Kicad/Images of gerbers/b variant.PNG

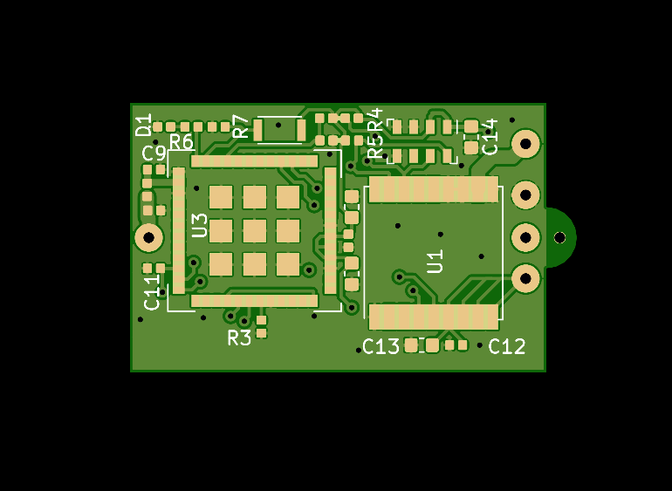
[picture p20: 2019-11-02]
hardware/Kicad/Images of gerbers/a variant.PNG

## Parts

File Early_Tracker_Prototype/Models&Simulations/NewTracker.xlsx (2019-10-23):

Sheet: Overview
Imperial College Space Society
LoraWAN High Altitude Balloon Tracker
Data, Simulations and Models

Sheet: Cost
Imperial College Space Society
LoraWAN High Altitude Balloon Tracker
Cost Budget |  |  | unit Price | Total
 |  |  | UKP inc VAT |  | Source
Component | Type | Quantity
GPS Receiver | uBlox MAX8Q | 1 | 11.99 | 11.99 | Uputronics
GPS Antenna | Guitar Wire | 1 | 0 | 0
LoRaWAN | Murata ABZ | 1 | 0 | 15.98 | RS Components 144-2713
LoraWAN Antenna | Flexible Wire | 1 | 0 | 0
PCB | Custom | 1 | 0.65 | 0.65 | JLCPCB
USB Connector |  | 0 | 0 | 0
USB Protection |  | 0 | 0 | 0
Solar Cell |  | 6 | 0.0755 | 0.453 | https://www.aliexpress.com/item/32757770261.html
Super Capacitor |  | 1 | 0 | 0
Environment sensor | MS5607 | 1 | 3.43 | 3.43 | RS Components 893-7095
Attitude Sensor |  | 1 | 0 | 0
Power Control |  | 1 | 0 | 0
Programming Connector |  | 0 | 0 | 0
Solar Charger |  | 1 | 0 | 0
Power Supply |  | 1 | 0 | 0
 |  |  | Total | 32.503 | UK Pounds
* Based on One off component costs where possible

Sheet: Weight
Imperial College Space Society
LoraWAN High Altitude Balloon Tracker
Weight Budget |  |  | Unit Weight | Total Weight | Data
 |  |  | g | g |  | Source
Component | Type | Quantity
GPS Receiver | uBlox MAX8Q | 1 | 0.49 | 0.49 | Measured | Uputronics
GPS Antenna | Guitar Wire | 1 | 0 | 0
LoRaWAN | Murata ABZ | 1 | 0.45 | 0.45 | Measured | RS Components
LoraWAN Antenna | Flexible Wire | 1 | 0 | 0
PCB | Custom | 1 | 1.5 | 1.5 | Calculated | JLCPCB
USB Connector |  | 0 | 0 | 0
USB Protection |  | 0 | 0 | 0
Solar Cell |  | 6 | 0 | 0 | Measured | https://www.aliexpress.com/item/32757770261.html
Super Capacitor |  | 1 | 0 | 0 | Datasheet
Environment sensor | MS5607 | 1 | 0 | 0
Attitude Sensor |  | 1 | 0 | 0
Power Control |  | 1 | 0 | 0
Programming Connector |  | 0 | 0 | 0
Solar Charger |  | 1 | 0 | 0
Power Supply |  | 1 | 0 | 0
 |  |  | Total | 2.44 | g

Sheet: Power Consumption
Imperial College Space Society
LoraWAN High Altitude Balloon Tracker
Power Consumption
GPS | uBlox MAX8Q |  |  |  | From Data Sheet
Power Supply Voltage:
 | Min | 2.7 | Volts
 | Typical | 3 | Volts
 | Max | 3.6 | Volts
Backup Supply Voltage
 | Min | 1.4 | Volts
 | Typical | 3 | Volts
 | Max | 3.6 | Volts
Backup Battery Current
 | Typical | 20 | uA | For SW configured backup mode
 |  |  |  | Can be lower by using power switches
 |  |  |  | Not really worth it in Solar device
Operating Current
Acquisition | Typical | 19 | mA | at 3V
Tracking Continuous | Typical | 17 | mA | at 3V
Tracking Power Save | Typical | 4.7 | mA | at 3V
Maximum |  |  |  | at 3V
State Time estimates
Acquisition | Typical | 60 | sec
Tracking | Typical | 3 | sec
Ephemeris data when stored only lasts 4 hrs
Radio/Processor | Murata ABZ
Power Supply Voltage(USB used):
 | Min | 3 | Volts
 | Typical | 3.3 | Volts
 | Max | 3.6 | Volts
Power Supply Voltage(No USB):
 | Min | 2.4 | Volts
 | Typical | 3.3 | Volts
 | Max | 3.6 | Volts
Operating Current
Receive | Typical | 24 | mA | at 3V
Transmit | Typical | 36 | mA | 10dbm Tx
Transmit | Typical | 47 | mA | 14dbm Tx
Transmit | Typical | 128 | mA | 20dbm Tx
Processor only | Estimated | 10 | mA
Standby | Typical | 1.7 | mA | at 3V
State Time estimates
Receive | Typical | 5 | sec
Transmit | Typical | 2 | sec
Processor only | Typical | 30 | sec
Environment Sensor | MS5607
Power Supply Voltage:
 | Min | 1.8 | Volts
 | Typical | 3 | Volts
 | Max | 3.6 | Volts
Operating Current
Peak | Typical | 1.4 | mA
Standby | Typical | 0.14 | uA
State Time estimates
Peak | Typical | 10 | msec | Conversion

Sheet: Radio
Imperial College Space Society
LoraWAN High Altitude Balloon Tracker
Radio
Things Network Fair Access Policy |  |  | 30 | sec | Transmissions per 24hr day
Airtime Calculator | Link to Google Spreadsheet (https://docs.google.com/spreadsheets/d/1QvcKsGeTTPpr9icj4XkKXq4r2zTc2j0gsHLrnplzM3I/edit)
Size of telemetry String |  | 20 | bytes
Transmissions per day |  | SF7 | 400 |  | 30 | per daylight hour
 |  | SF12 | 15 |  | 1 | per daylight hour

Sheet: Power Source
Imperial College Space Society
LoraWAN High Altitude Balloon Tracker
Power Source
Solar Cell Specification |  |  | http://vi.raptor.ebaydesc.com/ws/eBayISAPI.dll?ViewItemDescV4&item=183991095461
Polycrystaline Silicon
Size per cell |  | 19 | mm | by | 52 | mm
Efficiency |  | 17.4 | %
Maximum Power |  | 170 | mW
Maximum Voltage |  | 0.512 | V
Maximum Current |  | 340 | mA
Short Circuit Current |  | 340 | mA
Open Circuit Voltage |  | 0.564 | V
Life |  | 5 | Years
Results of first tests of a 4 cell series connected array
Solar Cell Tests
Load
R | V | W | mA
1000000 | 2.26 | 5.1076e-06 | 2.26e-06 |  | Condition: very dull, Autumn day
100 | 1.85 | 0.034225 | 0.0185
10 | 0.48 | 0.02304 | 0.048
Load
R | V | W | mA
1000000 | 2.26 | 5.1076e-06 | 2.26e-06 |  | Condition: bright Autumn day
100 | 2.244 | 0.05035536 | 0.02244
10 | 1.4 | 0.196 | 0.14
Results of first tests of a 6 cell series connected array
Solar Cell Tests
Load
R | V | W | mA
1000000 | 3.63 | 1.31769e-05 | 3.63e-06 |  | Condition: bright Autumn day
0 | 0 | 0 | 140 |  | Condition: bright Autumn day
Load
R | V | W | mA
1000000 | 3.45 | 1.19025e-05 | 3.45e-06 |  | Condition: very dull, Autumn day
0 | 0 | 0 | 48 |  | Condition: very dull, Autumn day
50 | 3.35 | 0.22445 | 0.067 |  | Condition: dull, Autumn day

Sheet: Dimensions
Dimensions

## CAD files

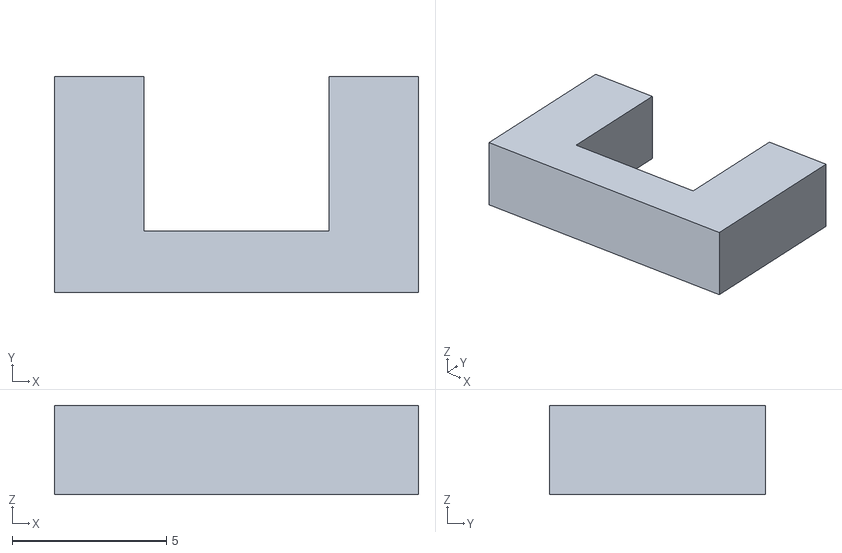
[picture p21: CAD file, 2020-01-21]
hardware/Fusion360/1.1 clip/HAB2Bb.STL
11.8 x 7.00 x 2.90

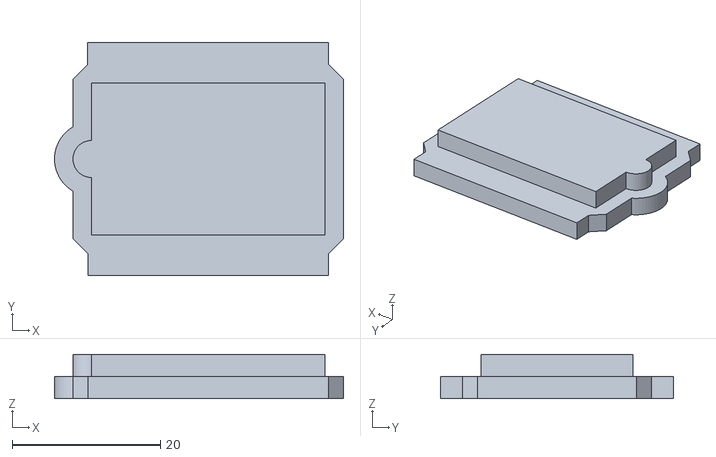
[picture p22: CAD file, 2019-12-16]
hardware/Fusion360/1.1a Jig/LoRa Jig Top Cap.stl
39.0 x 31.5 x 6.00

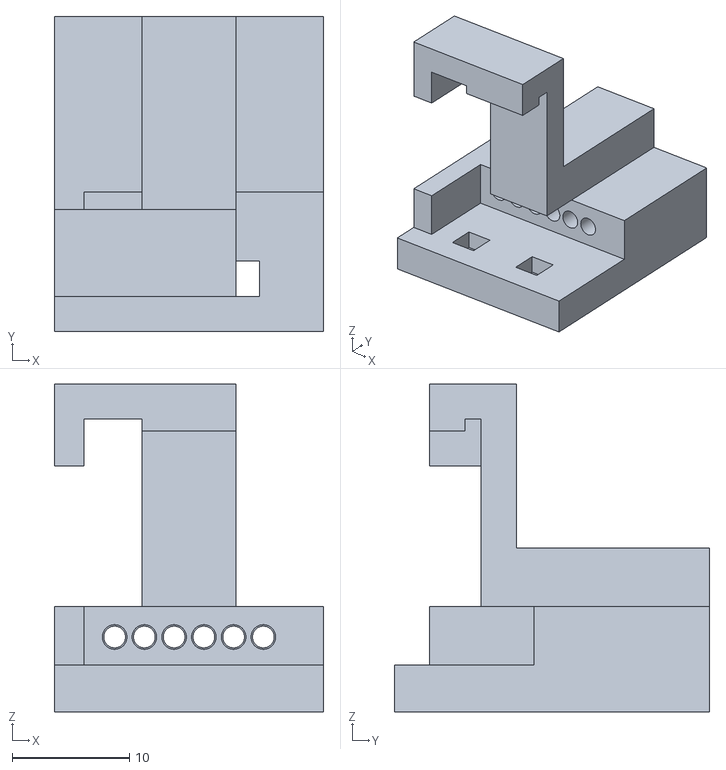
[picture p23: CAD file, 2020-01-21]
hardware/Fusion360/1.1 clip/HabB2a.STL
23.0 x 26.9 x 28.0

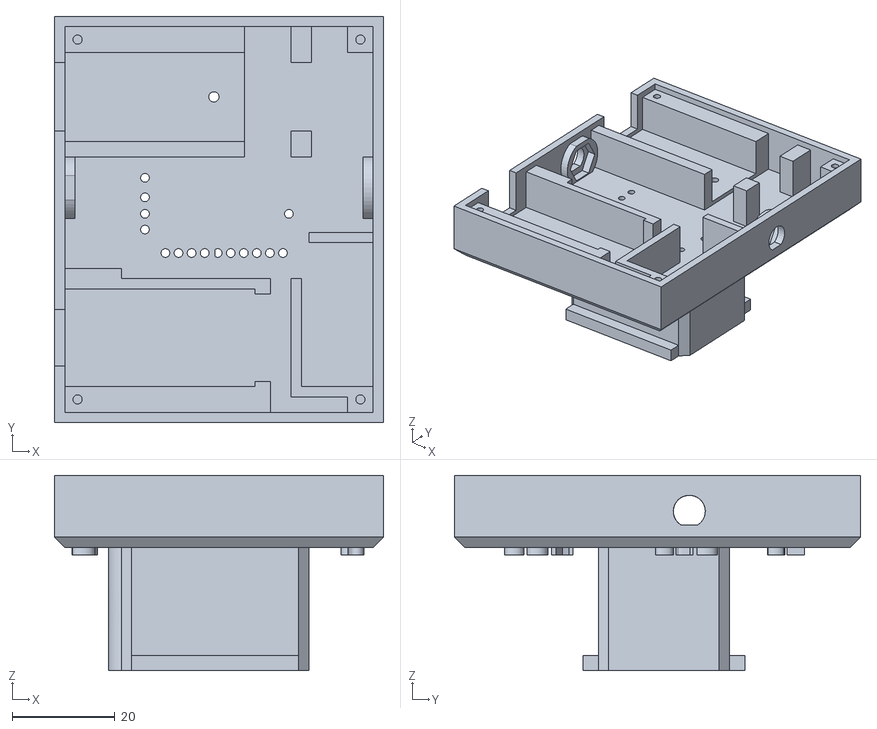
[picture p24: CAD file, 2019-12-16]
hardware/Fusion360/1.1a Jig/LoRa Jig Body.stl
64.0 x 79.0 x 38.0

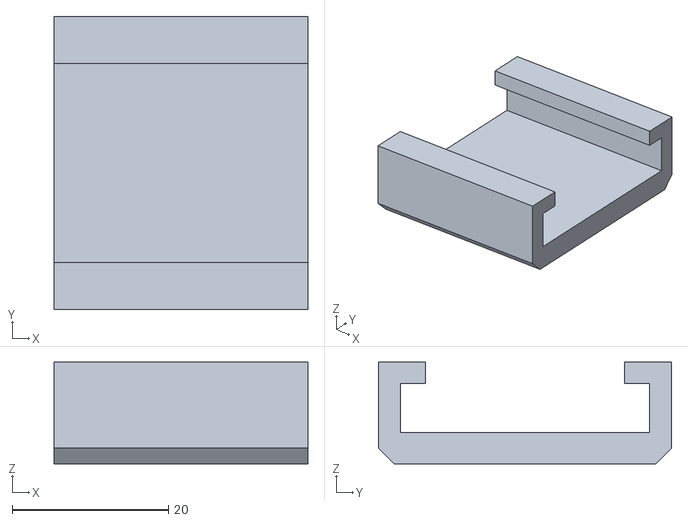
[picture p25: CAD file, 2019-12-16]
hardware/Fusion360/1.1a Jig/LoRa Jig Clip.stl
32.5 x 37.5 x 13.0

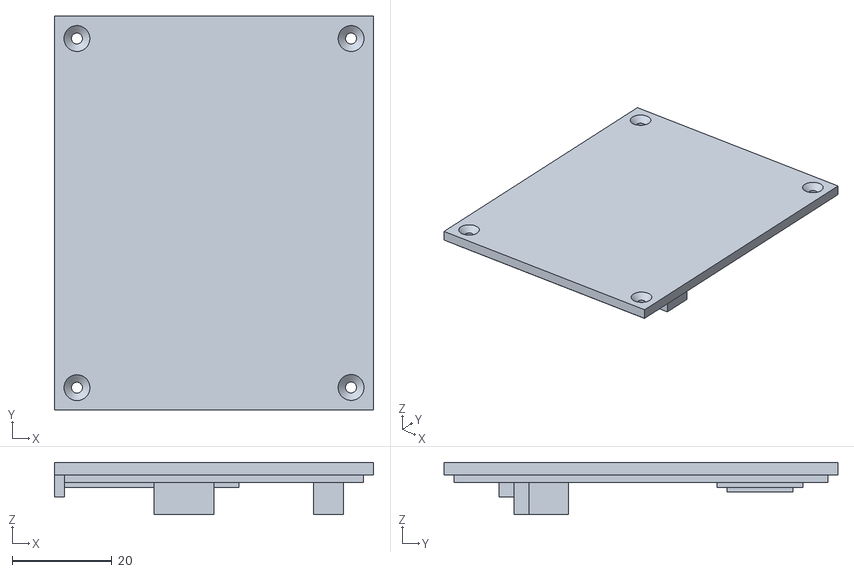
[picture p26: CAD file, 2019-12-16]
hardware/Fusion360/1.1a Jig/LoRa Jig Bottom.stl
64.0 x 79.0 x 10.5

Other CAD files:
hardware/Fusion360/1.1a Jig/PicoTracker Lora Jig_1.1a v7.f3d

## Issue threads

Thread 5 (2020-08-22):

Batt voltage check happens very little load; does not measure under gps load

MedadRufus, 2020-08-22:
This means that batt voltage is measured very high, but when gps powers up, due to the high current consumption, the solar cells cannot sustain that current and voltage falls. Find what this voltage is.

MedadRufus, 2020-09-01:
send down two batt voltages. one under load and one with no load. we have two bytes of data

MedadRufus, 2020-09-02:
fixed in #14

Closed 2020-09-02.

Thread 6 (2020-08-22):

At low solar irradiance, mcu would brownout before transmitting

MedadRufus, 2020-08-22:
Ideally, we the tracker to tx all the way down to 2.2V solar voltage. However, when the gps is powered on, due to limited current from cells, it would brownout. On restart, it will AGAIN try to power up the gps, causing a brownout. Repeat infintiely.

MedadRufus, 2020-09-02:
Not a huge problem. Also, if it were to tx in the morning without a gps fix, there is no garantee that it will be transmitting on the frequency suitable to local regulations.

Closed 2020-09-02.

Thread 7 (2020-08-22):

Cannot power cycle GPS

MedadRufus, 2020-08-22:

MedadRufus, 2020-08-27:
fixed in  pull request Revert to old recovery #9

Closed 2020-08-27.

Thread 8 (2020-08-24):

if gps does not get a fix/respond, cut power to it during the tx phase

MedadRufus, 2020-08-24:

MedadRufus, 2020-08-27:
gps stuck issue fixed in #9

Closed 2020-08-27.

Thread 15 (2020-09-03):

GPS not going into low power mode if it has an i2c failure during gps checking.

MedadRufus, 2020-09-03:
Do the full GPS reinit, setting up the power save config, and putting into low power mode, as we do at the beginning.

MedadRufus, 2020-09-05:
not true

Closed 2020-09-05.

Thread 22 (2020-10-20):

GPS is getting power cycled too much when power is low

MedadRufus, 2020-10-20:

MedadRufus, 2020-10-30:
This may be an issue during sun rise. It may be taking too long to get a GPS fix in the morning. What if we never reset the GPS? just let it carry on.

MedadRufus, 2020-12-30:
Does not seem to be a problem for ICSPACE23.

Closed 2020-12-30.

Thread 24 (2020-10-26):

Send 9 locations in each transmission: Current location and 8 other past locations

MedadRufus, 2020-10-26:
This is because, global LoRaWAN coverage is very poor and only on a few occasions do we hear from it.
Tasks to carry out:

- [x]  encode 4 locations and their timestamps in a single 26 byte transmission

- [x] save past locations to Non Volatile memory

- [x] Tacktically send past info that contains the most info about the flight path. One option is the
Van der Corput sequence.

- [x]  Compress the data such that it can be sent in 26 bytes. e.g. send timestamps as time deltas of the current time, and use other forms of compression.

- [ ] Test if it successfully manages the overflow of eeprom

- [ ] Ensure that the device will tx 120 byte long messages over US,AU and JP

- [x] test next_LCG, even when all elements have been generated

- [ ] Fix poor implementation of LCG

MedadRufus, 2020-10-31:
Based on the lormac region spec, the minimum packet size does not appear to be 26 or 30 bytes. Actually, it is closer to 240 over US915 and similar for EU868 when using DR3.

MedadRufus, 2020-10-31:
When it comes to prioritising transmissions, I would use a combination of

1. Coverage maps, mainly over Europe
2. Listening for downlinks(messages from gateways to end node) to detect if the tracker is being heard
as inputs to determine what has to be transmitted.
3. Try to send up a message to the tracker telling it what info has been received and what has not been received; where we are missing info in the timeline. The tracker can delete the times when it has already be listened and not transmit them down again.

Then I would transmit position for each day, then the second position for each day, third and so on. The first position for the day will be at midday, based on highest position of the sun. Then the next two positions will be the first and last position fixes for the day. The subsequent positions will be positions between First and midday packet, and between midday and final packet for the day.

I think in total, per day, we need to only store 5 positions.

MedadRufus, 2020-10-31:
Each packet should contain the info from one position per day from the last 4 days. Or the last 8 days, but alternate days. It appears that we are restricted to transmitting only 4 positions, in addition to the current one in each packet. Unless we use larger packet sizes, which I don't mind using. I will stick to the national regulations, but sticking to the TTN limit of 30s airtime per day is much harder.

MedadRufus, 2020-10-31:
Developing on the previous comment, each packet should transmit 8 archived positions, one for the 8 past days each, along with the current fix. For each past day, the position will be a random position from that day without repeating unless all have been transmitted. i.e. the position can be from any time in the day.

Therefore, as the balloon comes back over Europe, with each transmission, we will get a more and more clear picture of where it was for the last 8 days.

We can use the GPS timestamps to tell the tracker the start and end of each day.

MedadRufus, 2020-10-31:
My estimate indicates that current position along with pressure/temp etc can fit in 70 bits.
Each archived position that contains position and time fits in 40 bits.
The proposed packet will therefore contain (70 + 40 * 8) bits which is 390 bits which fits in 49 bytes.

MedadRufus, 2020-11-02:
Be default, the tracker will transmit 8 archieved positions of the _last_  8 days. However, if we need to get info from even earlier than the past 8 days, e,g, 15 days ago, we can send a downlink to the tracker that will switch it to transmitting the 8 days before the required days.

MedadRufus, 2020-11-02:
Save a whole position fix+ time in eeprom as a fixed size (e.g. 6 bytes). To iterate through it, go from 6 bytes to the next 6 bytes etc. Allocate a few kb of eeprom for this use. Overwrite from start when this space is fully filled. Prefereably add a checksum at the end of each saved position to ensure uncorrupted data.
Its important to make the space allocated to the data a multiple of the fixed size. e.g. if the size is 6 bytes, the space allocated should be n*6 bytes.

MedadRufus, 2020-11-02:
Perhaps, make a table holding the info about how many position fixes there are for each day, so that a random position fix can be retrieved efficiently.

MedadRufus, 2020-11-03:
Timestamp should be days since 1/1/2020 and hour, minute, second of day.
Or, ITOW + week number

MedadRufus, 2020-11-03:
I was thinking about the compression of flight path data. What if we encode all the archived flight path in a polynomial, and send only the coefficients.
With each new transmission, the polynomial would approximate the flight path better.
This will cause a loss of accuracy, but give a big picture of the flight path.

MedadRufus, 2020-11-09:
Simplifying the whole thing, we get it to send the last 8 position randomly picked from the last `n` positions. We can add additional options to send a downlink to the endnode to send more than 8 positions, pick from a larger pool of past positions and have a different offset position. i.e. instead of selecting from the last 20 positions, ignore the last 10 positions and pick from the 20 before that.

So in summary the options are:
1. number of positions to send in a single packet
2. how many positions to select from
3. offset of positions

All these can be specified from an downlink but will have a default.

MedadRufus, 2020-11-20:
TODO
- [ ] integrate the string builder into the main program
- [ ] fill the string builder with info
- [ ] get time since epoch from GPS. need to test in hardware.

MedadRufus, 2020-11-21:
TODO

- [ ] add number of resets to the sensor_t

- [ ] Add data received flag to it as well

- [ ] Add options to configure playback params via and downlink(message from ground to tracker)

- [ ] Add option to save position every 30 minutes

- [ ] Prevent sending position two times over

- [ ] Send one position from each day in the packet

MedadRufus, 2020-11-21:
verify save eeprom fcnt

MedadRufus, 2020-11-21:
- [ ] Implement Van Der Corput Sequence for sending down data

Closed 2020-11-27.

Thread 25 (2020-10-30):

Make tracker transmit at a lower sun elevation in the morning

MedadRufus, 2020-10-30:
It is estimated that the tracker transmits for the first time at only 23 degrees sun elevation. However, as the sun goes down, it is able to tx all the way to 12 degrees.

Its important to maximise the time it transmits

MedadRufus, 2020-10-30:
First data on ICSPACE21 on day 2
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

MedadRufus, 2020-10-30:
I confirm that the balloon is waking up at 12.89 degrees sun elevation. Similar to elevation when sun is setting.
Below is the calculation for when the sun was rising on day 2 of ICSPACE21.
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

MedadRufus, 2020-10-30:
The Sun elevation was at 15.57 degrees elevation at the end of that day.
Info at 8848m altitude, at 15:02 UTC on 5 September 2020 at position 45.5146,28.2977
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

MedadRufus, 2020-11-06:
We can optimise this by putting the mcu in low power mode, while GPS searches for first fix of day, to save a few mA. Around 6mA.

MedadRufus, 2020-11-16:
closed in favour of #32

Closed 2020-11-16.

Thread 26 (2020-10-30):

Some packets over US915 have no data

MedadRufus, 2020-10-30:
The raw logs are here

```json
[Wed, 28 Oct 2020 13:44:37] DEBUG message:Received PUBLISH (d0, q0, r0, m0), 'icss_lora_tracker/devices/icspace22/up', ...  (471 bytes)
[Wed, 28 Oct 2020 13:44:37] INFO b'{"app_id":"icss_lora_tracker","dev_id":"icspace22","hardware_serial":"00B76CF36C7CFA8A","port":0,"counter":2220,"payload_raw":null,"metadata":{"time":"2020-10-28T13:44:37.129959782Z","frequency":904.6,"modulation":"LORA","data_rate":"SF8BW500","airtime":20608000,"coding_rate":"4/5","gateways":[{"gtw_id":"eui-647fdafffe009962","timestamp":2283517889,"time":"","channel":18,"rssi":-107,"snr":-10.5,"rf_chain":0,"latitude":48.12364,"longitude":-78.09939,"altitude":397}]}}'
[Wed, 28 Oct 2020 14:38:24] DEBUG message:Received PUBLISH (d0, q0, r0, m0), 'icss_lora_tracker/devices/icspace22/up', ...  (678 bytes)
[Wed, 28 Oct 2020 14:38:24] INFO b'{"app_id":"icss_lora_tracker","dev_id":"icspace22","hardware_serial":"00B76CF36C7CFA8A","port":99,"counter":2245,"payload_raw":"AHMJoAFn/7wCiAfXY/QIXA8NIAMCJiYEAQs=","payload_fields":{"analog_in_3":97.66,"barometric_pressure_0":246.4,"digital_out_4":11,"gps_2":{"altitude":9864,"latitude":51.3891,"longitude":-78.4292},"temperature_1":-6.8},"metadata":{"time":"2020-10-28T14:38:24.185519511Z","frequency":904.6,"modulation":"LORA","data_rate":"SF8BW500","airtime":38528000,"coding_rate":"4/5","gateways":[{"gtw_id":"eui-647fdafffe009962","timestamp":1215593121,"time":"","channel":18,"rssi":-109,"snr":-8,"rf_chain":0,"latitude":48.12367,"longitude":-78.09937,"altitude":399}]}}'
[Wed, 28 Oct 2020 14:49:31] DEBUG message:Received PUBLISH (d0, q0, r0, m0), 'icss_lora_tracker/devices/icspace22/up', ...  (468 bytes)
[Wed, 28 Oct 2020 14:49:31] INFO b'{"app_id":"icss_lora_tracker","dev_id":"icspace22","hardware_serial":"00B76CF36C7CFA8A","port":0,"counter":2251,"payload_raw":null,"metadata":{"time":"2020-10-28T14:49:31.104492242Z","frequency":904.6,"modulation":"LORA","data_rate":"SF8BW500","airtime":20608000,"coding_rate":"4/5","gateways":[{"gtw_id":"eui-647fdafffe009962","timestamp":1882515809,"time":"","channel":18,"rssi":-106,"snr":-9,"rf_chain":0,"latitude":48.12365,"longitude":-78.09937,"altitude":389}]}}'
[Wed, 28 Oct 2020 15:07:51] DEBUG message:Received PUBLISH (d0, q0, r0, m0), 'icss_lora_tracker/devices/icspace22/up', ...  (470 bytes)
[Wed, 28 Oct 2020 15:07:51] INFO b'{"app_id":"icss_lora_tracker","dev_id":"icspace22","hardware_serial":"00B76CF36C7CFA8A","port":0,"counter":2260,"payload_raw":null,"metadata":{"time":"2020-10-28T15:07:51.137357052Z","frequency":904.6,"modulation":"LORA","data_rate":"SF8BW500","airtime":20608000,"coding_rate":"4/5","gateways":[{"gtw_id":"eui-647fdafffe009962","timestamp":2982558473,"time":"","channel":18,"rssi":-107,"snr":-3.8,"rf_chain":0,"latitude":48.12365,"longitude":-78.09939,"altitude":395}]}}'
[Wed, 28 Oct 2020 15:39:55] DEBUG message:Received PUBLISH (d0, q0, r0, m0), 'icss_lora_tracker/devices/icspace22/up', ...  (678 bytes)
[Wed, 28 Oct 2020 15:39:55] INFO b'{"app_id":"icss_lora_tracker","dev_id":"icspace22","hardware_serial":"00B76CF36C7CFA8A","port":99,"counter":2276,"payload_raw":"AHMF5wFn/80CiAfXwPRecQ8aBAMCJCUEAQg=","payload_fields":{"analog_in_3":92.53,"barometric_pressure_0":151.1,"digital_out_4":8,"gps_2":{"altitude":9897,"latitude":51.3984,"longitude":-76.2255},"temperature_1":-5.1},"metadata":{"time":"2020-10-28T15:39:55.104081611Z","frequency":904.6,"modulation":"LORA","data_rate":"SF8BW500","airtime":38528000,"coding_rate":"4/5","gateways":[{"gtw_id":"eui-647fdafffe009962","timestamp":611557965,"time":"","channel":18,"rssi":-107,"snr":-6.5,"rf_chain":0,"latitude":48.12366,"longitude":-78.09938,"altitude":391}]}}'
[Wed, 28 Oct 2020 15:42:24] DEBUG message:Received PUBLISH (d0, q0, r0, m0), 'icss_lora_tracker/devices/icspace22/up', ...  (466 bytes)
[Wed, 28 Oct 2020 15:42:24] INFO b'{"app_id":"icss_lora_tracker","dev_id":"icspace22","hardware_serial":"00B76CF36C7CFA8A","port":0,"counter":2277,"payload_raw":null,"metadata":{"time":"2020-10-28T15:42:24.125170512Z","frequency":904.6,"modulation":"LORA","data_rate":"SF8BW500","airtime":20608000,"coding_rate":"4/5","gateways":[{"gtw_id":"eui-647fdafffe009962","timestamp":760577143,"time":"","channel":18,"rssi":-101,"snr":-6,"rf_chain":0,"latitude":48.12366,"longitude":-78.0994,"altitude":390}]}}'
```

MedadRufus, 2020-10-30:
Pretty printing Json

```json

{
  "app_id": "icss_lora_tracker",
  "dev_id": "icspace22",
  "hardware_serial": "00B76CF36C7CFA8A",
  "port": 0,
  "counter": 2220,
  "payload_raw": null,
  "metadata": {
    "time": "2020-10-28T13:44:37.129959782Z",
    "frequency": 904.6,
    "modulation": "LORA",
    "data_rate": "SF8BW500",
    "airtime": 20608000,
    "coding_rate": "4/5",
    "gateways": [
      {
        "gtw_id": "eui-647fdafffe009962",
        "timestamp": 2283517889,
        "time": "",
        "channel": 18,
        "rssi": -107,
        "snr": -10.5,
        "rf_chain": 0,
        "latitude": 48.12364,
        "longitude": -78.09939,
        "altitude": 397
      }
    ]
  }
}

{
  "app_id": "icss_lora_tracker",
  "dev_id": "icspace22",
  "hardware_serial": "00B76CF36C7CFA8A",
  "port": 99,
  "counter": 2245,
  "payload_raw": "AHMJoAFn/7wCiAfXY/QIXA8NIAMCJiYEAQs=",
  "payload_fields": {
    "analog_in_3": 97.66,
    "barometric_pressure_0": 246.4,
    "digital_out_4": 11,
    "gps_2": {
      "altitude": 9864,
      "latitude": 51.3891,
      "longitude": -78.4292
    },
    "temperature_1": -6.8
  },
  "metadata": {
    "time": "2020-10-28T14:38:24.185519511Z",
    "frequency": 904.6,
    "modulation": "LORA",
    "data_rate": "SF8BW500",
    "airtime": 38528000,
    "coding_rate": "4/5",
    "gateways": [
      {
        "gtw_id": "eui-647fdafffe009962",
        "timestamp": 1215593121,
        "time": "",
        "channel": 18,
        "rssi": -109,
        "snr": -8,
        "rf_chain": 0,
        "latitude": 48.12367,
        "longitude": -78.09937,
        "altitude": 399
      }
    ]
  }
}

{
  "app_id": "icss_lora_tracker",
  "dev_id": "icspace22",
  "hardware_serial": "00B76CF36C7CFA8A",
  "port": 0,
  "counter": 2251,
  "payload_raw": null,
  "metadata": {
    "time": "2020-10-28T14:49:31.104492242Z",
    "frequency": 904.6,
    "modulation": "LORA",
    "data_rate": "SF8BW500",
    "airtime": 20608000,
    "coding_rate": "4/5",
    "gateways": [
      {
        "gtw_id": "eui-647fdafffe009962",
        "timestamp": 1882515809,
        "time": "",
        "channel": 18,
        "rssi": -106,
        "snr": -9,
        "rf_chain": 0,
        "latitude": 48.12365,
        "longitude": -78.09937,
        "altitude": 389
      }
    ]
  }
}

{
  "app_id": "icss_lora_tracker",
  "dev_id": "icspace22",
  "hardware_serial": "00B76CF36C7CFA8A",
  "port": 0,
  "counter": 2260,
  "payload_raw": null,
  "metadata": {
    "time": "2020-10-28T15:07:51.137357052Z",
    "frequency": 904.6,
    "modulation": "LORA",
    "data_rate": "SF8BW500",
    "airtime": 20608000,
    "coding_rate": "4/5",
    "gateways": [
      {
        "gtw_id": "eui-647fdafffe009962",
        "timestamp": 2982558473,
        "time": "",
        "channel": 18,
        "rssi": -107,
        "snr": -3.8,
        "rf_chain": 0,
        "latitude": 48.12365,
        "longitude": -78.09939,
        "altitude": 395
      }
    ]
  }
}
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
MedadRufus, 2020-10-30:
The single channel txing does not explain why the transmissions were limited.
According to [Disk91](https://www.disk91.com/2019/technology/lora/lorawan-in-us915-zone/), the only limitation is it can tx for at most 400ms in 20 seconds:

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

MedadRufus, 2020-10-30:
The no data packet can be replicated in EU868 by setting the packet size to be very big i.e 60 bytes. Data rate was set to DR_0
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

lorawan_regional_parameters_v1.0.3reva_0 says that max bytes is 59.
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

MedadRufus, 2020-10-30:
However, Every single tx in EU868 simulation has the no data packet. However, we have seen over US915 that it is intermittent; 4 out of 6 packets had no data.

MedadRufus, 2020-10-31:
I believe that the first tx from each us915 transmission is a null one. This is based on using the debugger to trace. Not sure why. However, from flight data, we find that this null transmission happens often. null happend 4 times out of 6 received transmissions. Solar Voltage is 3.6V and 3.8V on the two transmissions. I would expect it to be higher, though I did not verify the height of the sun.

I suspect that the device is resetting often.

My first suspicion is because of the wider bandwidth used on US915 than in EU868 and AS923. In EU868 and AS923, bandwidth is 125khz while in US915, bandwidth is 500khz.

One solution is to switch to using DR3 instead of DR4 as default data rate. This will make the tracker tx on 125khz bandwidth in the US. This will improve SNR performace as well.

The code seems to show no indication of this intermittent null/not null transmission. It seems to do one null transmission and then all other transmission happen with a filled frame.

lorawan_regional_parameters_v1.0.3revA indicates that max payload size for DR3 and 4 is 250 bytes. Plenty of space.
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

MedadRufus, 2020-11-06:
Richard will be doing some tests with the B-L072-LRWAN1 dev board on US915 frequencies.

MedadRufus, 2020-11-16:
When using US915, the first frame after reset **_ALWAYS_** goes through this point: [code link](https://github.com/ImperialSpaceSociety/picotracker-Lora/blob/25bee817ff1dcbcec709a1b622591d05547d55bf/Software/Middlewares/Third_Party/LoRaWAN/Core/lora.c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). The comment there says
```c
// Send empty frame in order to flush MAC commands
```

This happens everying single time when transmitting on US915 but never when using EU868. Note that the second and beyond frame in US915 does not hit this breakpoint.

What I think is happening is the tracker is resetting often, possibly during the tx phase. This may be due to the higher power transmissions over US915.

looking at the region.h file for EU868 and US915, we see that max EIRP for EU868 is `16.0f` vs max ERP `30.0f` for US915. Note that the definition for EIRP and ERP is a little different.
```c
/*!
 * Default Max EIRP
 */
#define EU868_DEFAULT_MAX_EIRP                      16.0f

/*!
 * Default Max ERP
 */
#define US915_DEFAULT_MAX_ERP                      30.0f
```

MedadRufus, 2020-11-16:
90% sure of reset happening. The US915 TX power is much higher

MedadRufus, 2020-11-16:
This is the smoking gun.
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
When we plot elapsed time from previous tranmission, we find that all transmission with empty frames(in red dots) have had an elapsed time from previous transmission of more than 107 seconds. The values range from 149 -181 seconds. There is some variation in this time period. This can be explained by the time taken for the GPS to get its first fix after a full power cycle after a reset of the MCU. Only after the GPS fix does it do its first transmission after reset.

On the other hand, tranmissions with data(in blue) all have an elapsed time of either 107 seconds or a multiple of this time period, taking into accound lost packets due to poor reception.

It is however a mystery why it has a standard period between tranmissions of 107 seconds while it is programmed to be 120 seconds. It may be due to extreme drift of the internal 32Khz RC oscillator that provides this timing.

MedadRufus, 2020-11-16:
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
The data from the next day looks more interesting. We have a lot more empty packets. We have a lot more variation in elapsed time between transmissions. Indeed due to poorer reception in North Dakota, we may be missing quite a few packets.

However, this could ALSO be due to less sunlight at this latitude compared to the previous day's latitude. Less sunlight may be causing it to have less current, and hence more likely to reset.

MedadRufus, 2020-11-16:
Its definately browning out due to high power transmissions over US915. Simple solution is to reduce tx power over US915.

Closed 2020-11-18.

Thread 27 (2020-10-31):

Put in a counter to keep track of resets

MedadRufus, 2020-10-31:
helps to keep tracker of resets to solve #26

MedadRufus, 2020-11-27:
fixed in #29

Closed 2020-11-27.

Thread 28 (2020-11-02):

The rx window timings may be off due to clock drift

MedadRufus, 2020-11-02:
On ICSPACE19, for several days, the tracker failed to receive a packet from gateways on the ground to complete a join request. It made many attempts. I suspect its due to the timings of the RX window being off due to clock drift.

The clock source for this timing is a Low Speed External crystal which is not temperature compensating. The timing window needs to be accurate to within a few milliseconds.

One solution is to use the GPS 1 PPS clock input to caliberate the crystal.

MedadRufus, 2020-11-02:
the clock needs to be at least stable to 1 parts per thousand. At most 1 millisecond off.

The RX window has to open within 1millisecond of the specified time.

The first rx window in happens 1 second after tx and the second window happens 2 seconds after tx

But looking at these numbers, it it simply has to have a frequency stablility of 1 parts per 2000. Even a normal crystal oscilator should be able to provide that. 500 parts per million.

Closed 2020-11-02.

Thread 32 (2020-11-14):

Lower power consumption by ensuring that both GPS and MCU are not running in high power at same time

MedadRufus, 2020-11-14:
Currently, During a GPS fix search, both GPS and MCU are running in full power. GPS consumes around 40mA while MCU draws around 7-10mA. If I put the mcu to low power while the GPS searches, it will reduce the max power draw, hence allowing for the tracker to work at an even lower sun elevation.

Current record is 8 degrees sun elevation wake up. Can it be lowered even further?

MedadRufus, 2020-12-28:
Use timers to schedule the gps fix check. Otherwise, stay in ultra low power mode. Must create state machine like `barometer_operate(...)` like in this example: https://android.googlesource.com/kernel/mediatek/+/android-mediatek-sprout-3.10-marshmallow-mr1/drivers/misc/mediatek/barometer/ms5607/ms5607.c

MedadRufus, 2020-12-28:
Can poll GPS every 20 seconds, and stay in deep sleep then.

Closed 2021-09-25.

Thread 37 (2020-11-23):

There are some packets received by gateways that have the wrong timestamp.

MedadRufus, 2020-11-23:
These packets are repeat packets, with the same raw data. However, besides the same raw data, it appears like a new packet. It arrives a minute or two after the original one. An example is here:

**Original**:
```json

{
  "app_id": "icss_lora_tracker",
  "dev_id": "icspace22",
  "hardware_serial": "00B76CF36C7CFA8A",
  "port": 99,
  "counter": 267,
  "payload_raw": "AHMJfwFn/1MCiAfMdwC5AhA3kAMCJycEAQ4=",
  "payload_fields": {
    "analog_in_3": 100.23,
    "barometric_pressure_0": 243.1,
    "digital_out_4": 14,
    "gps_2": {
      "altitude": 10628,
      "latitude": 51.1095,
      "longitude": 4.7362
    },
    "temperature_1": -17.3
  },
  "metadata": {
    "time": "2020-10-19T12:29:31.039467386Z",
    "frequency": 868.3,
    "modulation": "LORA",
    "data_rate": "SF8BW125",
    "airtime": 154112000,
    "coding_rate": "4/5",
    "gateways": [
      {
        "gtw_id": "eui-b827ebfffe6db3bd",
        "timestamp": 205982540,
        "time": "2020-10-19T12:29:30.024465Z",
        "channel": 1,
        "rssi": -114,
        "snr": -3,
        "rf_chain": 0,
        "latitude": 51.8014,
        "longitude": 4.68285,
        "altitude": 11
      },
      {
        "gtw_id": "eui-b827ebfffe53102e",
        "timestamp": 1879880300,
        "time": "2020-10-19T12:29:31.027671Z",
        "channel": 1,
        "rssi": -117,
        "snr": -9,
        "rf_chain": 0,
        "latitude": 51.88724,
        "longitude": 6.00133,
        "altitude": 13
      },
      {
        "gtw_id": "han_gateway_1",
        "timestamp": 202972836,
        "time": "2020-10-19T12:29:31Z",
        "channel": 0,
        "rssi": -107,
        "snr": 2,
        "rf_chain": 0,
        "latitude": 51.987885,
        "longitude": 5.951839,
        "altitude": 16
      },
      {
        "gtw_id": "eui-fcc23dfffe0f9843",
        "timestamp": 1151099324,
        "time": "2020-10-19T12:29:31.027172Z",
        "channel": 1,
        "rssi": -113,
        "snr": -4.5,
        "rf_chain": 0,
        "latitude": 51.9509,
        "longitude": 7.6384,
        "altitude": -1
      },
      {
        "gtw_id": "lorahil1",
        "timestamp": 3657876988,
        "time": "2020-10-19T12:29:31Z",
        "channel": 0,
        "rssi": -117,
        "snr": 1,
        "rf_chain": 0
      },
      {
        "gtw_id": "eui-b827ebfffeff3c5e",
        "timestamp": 3750551092,
        "time": "",
        "channel": 1,
        "rssi": -115,
        "snr": -8,
        "rf_chain": 0,
        "latitude": 51.58458,
        "longitude": 4.99626,
        "altitude": -262
      },
    ]
  }
}

```

**Fake packet**:
```json
{
  "app_id": "icss_lora_tracker",
  "dev_id": "icspace22",
  "hardware_serial": "00B76CF36C7CFA8A",
  "port": 99,
  "counter": 267,
  "payload_raw": "AHMJfwFn/1MCiAfMdwC5AhA3kAMCJycEAQ4=",
  "payload_fields": {
    "analog_in_3": 100.23,
    "barometric_pressure_0": 243.1,
    "digital_out_4": 14,
    "gps_2": {
      "altitude": 10628,
      "latitude": 51.1095,
      "longitude": 4.7362
    },
    "temperature_1": -17.3
  },
  "metadata": {
    "time": "2020-10-19T12:31:41.858983771Z",
    "frequency": 868.3,
    "modulation": "LORA",
    "data_rate": "SF8BW125",
    "airtime": 154112000,
    "coding_rate": "4/5",
    "gateways": [
      {
        "gtw_id": "syntouchmobile",
        "timestamp": 11787932,
        "time": "2020-10-19T12:31:41Z",
        "channel": 0,
        "rssi": -111,
        "snr": 0.5,
        "rf_chain": 0
      }
    ]
  }
}
```

MedadRufus, 2020-11-23:
I think the best way forward is to include the timestamp in the raw packet itself, based on GPS time, to get an unambiguous timestamp.

MedadRufus, 2020-11-23:
I belive the gateway in question, `syntouchmobile`, has not been configured properly. It is a rogue gateway.

MedadRufus, 2020-11-23:
Some gatways are rogue. Around 1 in 100. Not a high risk. Can be filtered out by checking if the raw packet is same as an earlier transmission.

MedadRufus, 2020-12-30:
Not a issue for the tracker. Its an issue for ttnhabhub bridge

Closed 2020-12-30.

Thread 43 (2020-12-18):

Lots of empty packets are being sent

MedadRufus, 2020-12-18:
Looks like the tracker is being reset between transmissions. This is based on the reset count field.
## Solutions to fix it:
* Fix the hardware. Maybe too little current is coming from the solar cells
* Ensure that the very first tranmission after reset contains useful data. Fix the problem where the first transmission sends an empty frame.

MedadRufus, 2020-12-26:
fixed in #48

Closed 2020-12-26.

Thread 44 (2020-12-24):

Use better source of randomness

MedadRufus, 2020-12-24:
https://github.com/ImperialSpaceSociety/picotracker-Lora/blob/1f9c594074d1ada538eb58c4fedd44a725feb477/Software/Drivers/BSP/Components/ublox/playback.c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

This source of randomness updates only every 20 minutes, when a new position is saved to eeprom. So it could be the same value for 20 minutes, and with resets within the 20 minutes, the LGC sequence will be identical. Which means, the past data sent down will be repeated. Bad.

MedadRufus, 2020-12-26:
fixed in #49

Closed 2020-12-26.

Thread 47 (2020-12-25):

Double check if the GPS is going into low power mode

MedadRufus, 2020-12-25:
It seems like the GPS and radio are running at the same time. IT could be the cause of frequent browning out.
It looks like it can get a fix, but browns out during transmission. From past tests, both GPS and radio use the same current, so I don't expect it to brown out while radio transmits after a successful GPS fix.

Closed 2021-09-25.

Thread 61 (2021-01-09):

current eeprom address must be incremented in bsp.c

MedadRufus, 2021-01-09:

MedadRufus, 2021-01-11:
fixed in #65

Closed 2021-01-11.

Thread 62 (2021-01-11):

Consider the case where the GPS does not get a fix and transmits.

MedadRufus, 2021-01-11:
How will the time deltas be affected? If not fix, it will calculate abs(0 - x) minutes.  But if the gps got a fix earlier, it will return the previous time so delta will be calculated abs(earlier_time - x) minutes.

We can make it such that if no fix, force it to calculate (0 - x). And set a bit in transmission that fix not found.

Closed 2021-01-11.

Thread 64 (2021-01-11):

Absurd high altitude positions being recorded and transmitted to gnd

MedadRufus, 2021-01-11:
There are 16000m+ positions transmitted and recorded, while testing on the ground

MedadRufus, 2021-01-13:
Happens only in a GPS denied area(indoors). Not critical because it does not happen out doors. It is a mystery why it happens, even though I check if it has 5+ satellites, 3D fix and GPS_fix== OK.

Closed 2021-01-13.

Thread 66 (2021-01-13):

There are unexpected brownouts in ICSPACE23

MedadRufus, 2021-01-13:
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

This causes gaps between transmissions of several minutes. This is for ICSPACE23.

Launched 17 December 2020

MedadRufus, 2021-01-13:
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

This is for ICSPACE21

MedadRufus, 2021-01-13:
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
The Plot for ICSPACE22 on day 1 over EU. There is a lot more gaps in data. The only change in the code was to limit channels over US915, unrelated to anything over EU.

MedadRufus, 2021-01-13:
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

Plot for ICSPACE20.  No gaps at all!
Recorded on 22 August.

MedadRufus, 2021-01-22:
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
Plot for ICSPACE24. Lots of gaps between transmission. No clear clumping. But this was with smaller solar cells(19mm x 39mm vs 19mm x 52mm for previous flights).
Recorded on 22 Jan 2021.

MedadRufus, 2021-04-20:
Its likely a power issue

MedadRufus, 2021-04-20:
Nothing can be done about it, except to reduce peak current consumption and having more sunlight.

MedadRufus, 2021-04-20:
#32 could improve things

MedadRufus, 2021-04-29:
ICSPACE23 and 24 had tilted solar cells, which contributes to the brownouts on each rotation. Earlier flights were held level

Closed 2021-04-20.

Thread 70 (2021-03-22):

use the loramac-node implementation and OTAA

MedadRufus, 2021-03-22:
This will make switching to TTN v3 possible, later in the future.

MedadRufus, 2021-03-22:
Make it do the join on the ground first.

MedadRufus, 2021-04-20:
Too much to verify. Don't do it

Closed 2021-04-20.

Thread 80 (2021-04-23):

ensure first transmission does not send 0 degress temperature

MedadRufus, 2021-04-23:

MedadRufus, 2021-04-28:
Fixed in e195ceaba68dc01ac17e0bdb45b6abec64d9d036

Closed 2021-04-28.

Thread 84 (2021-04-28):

Verify, if no fix is found and tx done, that we can read the past positions.

MedadRufus, 2021-04-28:
https://github.com/ImperialSpaceSociety/picotracker-Lora/blob/10fb4fc4cf8af3e2f90e448b1804dd0a574f9df0/Software/Drivers/BSP/Components/ublox/playback.c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

Delta time is calculated ok when `current_pos_ptr->minutes_since_epoch` is known. i.e. when gps fix is present. However, if no gps fix, are we able to recover the past positions? We will be dealing with roll overs since `current_pos_ptr->minutes_since_epoch` is unsigned, and likely the value will be negative when no fix.

For example, in the following log where no fix was found:
```
2021-04-28 00:48:53,612 INFO  TtnListener:96 - Message arrived on topic 'icss_lora_tracker/devices/icspace25_ttnv2_abp/up'
2021-04-28 00:48:53,621 INFO  TtnListener:102 - Message received: {"app_id":"icss_lora_tracker","dev_id":"icspace25_ttnv2_abp","hardware_serial":"00C7B88969018CF9","port":99,"counter":31,"payload_raw":"c4AABhMAAAAAAAC3HuD/0AGUY7ce4P85AYBjtx7g/9ABlGO3HuD/OQGAY7ce4P/QAZRjtx7g/zkBgGO3HuD/0AGUY7ce4P85AYBjtx7g/9ABlGO3HuD/OQGAY7ce4P/QAZRjtx7g/zkBgGO3HuD/0AGUYw==","metadata":{"time":"2021-04-28T00:48:53.397603706Z","frequency":868.3,"modulation":"LORA","data_rate":"SF7BW125","airtime":215296000,"coding_rate":"4/5","gateways":[{"gtw_id":"eui-58a0cbfffe800f4d","timestamp":11228355,"time":"2021-04-28T00:48:53.398327112Z","channel":0,"rssi":-75,"snr":9.75,"rf_chain":0}]}}
2021-04-28 00:48:53,622 INFO  PayloadDecoder:80 - Decoding 'CUSTOM_FORMAT_ICSS' message...
2021-04-28 00:48:53,623 INFO  ICSSPayload:123 -
Lon=-0.209712,Lat=51.530170,alt=118,ts=2021-04-10 07:56:53
Lon=-0.209712,Lat=51.530170,alt=79,ts=2021-04-10 08:16:53
Lon=-0.209712,Lat=51.530170,alt=118,ts=2021-04-10 07:56:53
Lon=-0.209712,Lat=51.530170,alt=79,ts=2021-04-10 08:16:53
Lon=-0.209712,Lat=51.530170,alt=118,ts=2021-04-10 07:56:53
Lon=-0.209712,Lat=51.530170,alt=79,ts=2021-04-10 08:16:53
Lon=-0.209712,Lat=51.530170,alt=118,ts=2021-04-10 07:56:53
Lon=-0.209712,Lat=51.530170,alt=79,ts=2021-04-10 08:16:53
Lon=-0.209712,Lat=51.530170,alt=118,ts=2021-04-10 07:56:53
Lon=-0.209712,Lat=51.530170,alt=79,ts=2021-04-10 08:16:53
Lon=-0.209712,Lat=51.530170,alt=118,ts=2021-04-10 07:56:53
Lon=-0.209712,Lat=51.530170,alt=79,ts=2021-04-10 08:16:53
Lon=-0.209712,Lat=51.530170,alt=118,ts=2021-04-10 07:56:53

2021-04-28 00:48:53,624 INFO  PayloadDecoder:88 - ICSS payload:playback_days=0, load_voltage=32, no_load_voltage=32, temp=19, lat=0.000000, lon=0.000000, alt=0, request_error=0, reset_cnt=6, pressure=0, numsats=0
2021-04-28 00:48:53,624 INFO  HabitatUploader:104 - Uploading for 1 receivers: $$icspace25_ttnv2_abp,31,00:48:53,0,19,0.000000,0.000000,0,32,32,0,6,0,0*FF37
2021-04-28 00:48:53,626 INFO  HabitatUploader:131 - Upload payload telemetry doc f3669b941ed617912307770b90b8a88742a7ffbf91b861f3c235d5585ece8260: {"data":{"_raw":"JCRpY3NwYWNlMjVfdHRudjJfYWJwLDMxLDAwOjQ4OjUzLDAsMTksMC4wMDAwMDAsMC4wMDAwMDAsMCwzMiwzMiwwLDYsMCwwKkZGMzcK"},"receivers":{"eui-58a0cbfffe800f4d":{"time_created":"2021-04-28T00:48:53.62183Z","time_uploaded":"2021-04-28T00:48:53.62183Z"}}}
2021-04-28 00:48:53,763 INFO  HabitatUploader:135 - Result payload telemetry doc f3669b941ed617912307770b90b8a88742a7ffbf91b861f3c235d5585ece8260: OK
```

The correct timestamps were meant to be:
```
2021-04-28 00:50:33,394 INFO  TtnListener:96 - Message arrived on topic 'icss_lora_tracker/devices/icspace25_ttnv2_abp/up'
2021-04-28 00:50:33,401 INFO  TtnListener:102 - Message received: {"app_id":"icss_lora_tracker","dev_id":"icspace25_ttnv2_abp","hardware_serial":"00C7B88969018CF9","port":99,"counter":32,"payload_raw":"c4AAJhC3HuD/GQG3HuD/OQEOALce4P/QASIAtx7g/zkBDgC3HuD/0AEiALce4P85AQ4Atx7g/9ABIgC3HuD/OQEOALce4P/QASIAtx7g/zkBDgC3HuD/0AEiALce4P85AQ4Atx7g/9ABIgC3HuD/OQEOAA==","metadata":{"time":"2021-04-28T00:50:33.177848671Z","frequency":868.1,"modulation":"LORA","data_rate":"SF7BW125","airtime":215296000,"coding_rate":"4/5","gateways":[{"gtw_id":"eui-58a0cbfffe800f4d","timestamp":111008931,"time":"2021-04-28T00:50:33.178787946Z","channel":0,"rssi":-72,"snr":9.75,"rf_chain":0}]}}
2021-04-28 00:50:33,402 INFO  PayloadDecoder:80 - Decoding 'CUSTOM_FORMAT_ICSS' message...
2021-04-28 00:50:33,404 INFO  ICSSPayload:123 -
Lon=-0.209712,Lat=51.530170,alt=79,ts=2021-04-28 00:36:33
Lon=-0.209712,Lat=51.530170,alt=118,ts=2021-04-28 00:16:33
Lon=-0.209712,Lat=51.530170,alt=79,ts=2021-04-28 00:36:33
Lon=-0.209712,Lat=51.530170,alt=118,ts=2021-04-28 00:16:33
Lon=-0.209712,Lat=51.530170,alt=79,ts=2021-04-28 00:36:33
Lon=-0.209712,Lat=51.530170,alt=118,ts=2021-04-28 00:16:33
Lon=-0.209712,Lat=51.530170,alt=79,ts=2021-04-28 00:36:33
Lon=-0.209712,Lat=51.530170,alt=118,ts=2021-04-28 00:16:33
Lon=-0.209712,Lat=51.530170,alt=79,ts=2021-04-28 00:36:33
Lon=-0.209712,Lat=51.530170,alt=118,ts=2021-04-28 00:16:33
Lon=-0.209712,Lat=51.530170,alt=79,ts=2021-04-28 00:36:33
Lon=-0.209712,Lat=51.530170,alt=118,ts=2021-04-28 00:16:33
Lon=-0.209712,Lat=51.530170,alt=79,ts=2021-04-28 00:36:33

2021-04-28 00:50:33,404 INFO  PayloadDecoder:88 - ICSS payload:playback_days=0, load_voltage=32, no_load_voltage=32, temp=16, lat=51.530170, lon=-0.209712, alt=71, request_error=0, reset_cnt=6, pressure=0, numsats=4
2021-04-28 00:50:33,413 INFO  HabitatUploader:104 - Uploading for 1 receivers: $$icspace25_ttnv2_abp,32,00:50:33,0,16,51.530170,-0.209712,71,32,32,0,6,4,0*FB6F
2021-04-28 00:50:33,414 INFO  HabitatUploader:131 - Upload payload telemetry doc 03b2fa52a2dde3bcf315ed7aeefd75c6af5bca24a09ed5a6698cbf241c7ab9e3: {"data":{"_raw":"JCRpY3NwYWNlMjVfdHRudjJfYWJwLDMyLDAwOjUwOjMzLDAsMTYsNTEuNTMwMTcwLC0wLjIwOTcxMiw3MSwzMiwzMiwwLDYsNCwwKkZCNkYK"},"receivers":{"eui-58a0cbfffe800f4d":{"time_created":"2021-04-28T00:50:33.401789Z","time_uploaded":"2021-04-28T00:50:33.401789Z"}}}
2021-04-28 00:50:33,588 INFO  HabitatUploader:135 - Result payload telemetry doc 03b2fa52a2dde3bcf315ed7aeefd75c6af5bca24a09ed5a6698cbf241c7ab9e3: OK
```

Closed 2022-03-05.

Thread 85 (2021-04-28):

If first fix not successful, tracker wastes time sleeping before getting new fix

MedadRufus, 2021-04-28:
In current code, whether it has a fix or not at the first fix, it will tx and and go to sleep for value defined by APP_DUTYCYCLE. Its 40 seconds. The problem arises when it has no fix, that it wastes valuable time on a rotation of the tracker sleeping. It must exploit the sun as much as possible, thus continueously searching for fix, especially when it does not have a fix after boot.

MedadRufus, 2021-04-28:
In stead, just increase the first fix timeout ot 2 x 180 seconds. Down side is, it will transmit as regularly as before

MedadRufus, 2021-09-27:
fixed in https://github.com/ImperialSpaceSociety/LoRaMac-node/pull/195

Closed 2021-09-27.

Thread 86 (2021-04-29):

Set up the GPS such that it is constantly getting fixes and updating latest internal position

MedadRufus, 2021-04-29:
Put the gps in low power only to do TX. Ensure TX is always on time.

Closed 2021-09-27.

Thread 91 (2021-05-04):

Switch Russian frequency plan to EU868

MedadRufus, 2021-05-04:
https://www.thethingsnetwork.org/docs/lorawan/frequencies-by-country/#r

MedadRufus, 2021-05-06:
Fixed in f504948954613a567521ca07baaed2bc7b5515d5

Closed 2021-05-06.

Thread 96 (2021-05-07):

Ensure the tracker does not waste getting a GPS fix because interval between tx was not short enough

MedadRufus, 2021-05-07:
Over the EU, 40 second interval is long enough(legal) with current packet size and DR5. However, over Japan, US, the datarate is DR4, so I don't know if the interval is long enough.

In the US, its not likely a problem because its not limited by dutycyle; experiments show that it can tx as often as it likes.

However, I have not tested for AS923.

MedadRufus, 2021-05-07:
Check it for AS923, with no antenna connected.

Closed 2021-09-27.

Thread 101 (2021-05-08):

[MAJOR] when new v1.0.2 application is made with US915 settings, no packets received in EU

MedadRufus, 2021-05-08:
On ttnv3, when a new  v1.0.2 application is made with US915 settings, no packets received in EU. Note that the same application can be created with EU868 settings and receive the data.

Changing region in teh interface to EU868 fails with the following error:
```
invalid value of field mac_state.current_parameters.rx2_data_rate_index

{
  "code": 3,
  "message": "error:pkg/networkserver:field_value (invalid value of field `mac_state.current_parameters.rx2_data_rate_index`)",
  "details": [
    {
      "@type": "type.googleapis.com/ttn.lorawan.v3.ErrorDetails",
      "namespace": "pkg/networkserver",
      "name": "field_value",
      "message_format": "invalid value of field `{field}`",
      "attributes": {
        "field": "mac_state.current_parameters.rx2_data_rate_index"
      },
      "correlation_id": "fc1143302d2e4fb7aac6a8d07da3afe4",
      "code": 3
    }
  ],
  "request_details": {
    "url": "/ns/applications/icss-lora-tracker/devices/icspace26-ttnv3-abp-us-v1-0-2",
    "method": "put",
    "stack_component": "ns"
  }
}
```

MedadRufus, 2021-05-08:
Only solution may be to switch ABP keys for each region, and make a seperate ABP application for each region.

MedadRufus, 2021-05-08:
Safest solution is to create ABP keys for each region. Each registration must have reset fcount enabled AT REGISTRATION. It apparently cannot be changed later.

Then when each region is selected, the keys should be changed along with it. Create look up table {region, network key, appsession key, id}

MedadRufus, 2021-05-08:
Changing region after creating the application does not work, although the interface indicates it.

MedadRufus, 2021-05-08:
This is the case for lorawan v1.0.3 as well

MedadRufus, 2021-07-10:
Just make new keys for each region

pimente, 2021-09-27:
Hello @MedadRufus
Congratulations for the success you have had so far.
This is quite impressing to have achieved circumnavigation with Lora only!

I am currently working on a similar project and have already achieved a successful flight in Europe with TTN3 and a Lora-E5 based tracker.
I am now trying to make the code work all over the world.
From the issues you have raised, it is not clear to me if we need to set up new ABP keys for each region.
This issue (the latest) seems to suggest that a key is needed for each region while issues [71](https://github.com/ImperialSpaceSociety/picotracker-Lora/issues/71) and [92](https://github.com/ImperialSpaceSociety/picotracker-Lora/issues/92) tend to suggest the opposite.

What final conclusion have you reached regarding this topic?

Your help is very much appreciated.

Cheers

MedadRufus, 2021-09-27:
My conclusion is that separate ABP keys are needed for each region. On the Things Network V3 console, I register one ABP device for each region, and dynamically change the ABP keys(DevAddr, FNwkSIntKey, SNwkSIntKey, NwkSEncKey, AppSKey) depending on each region.

In TTNv2, it was possible register a single ABP end node, and it would work in all regions(US915, EU868, AS923). This has been tested in flight. There was no requirement to specify which region the device was registered to in the interface.

However, on TTNv3, when registering the device, its required to specify which region parameters the end node uses. It appears to me that the set of ABP credentials generated for each region will only work on those region frequencies. I have tested this by:
1. registering an end node with US915 region
2. transmitting on EU868 frequencies and receiving on an EU868 gateway.

I get no packets on the TTNv3 console. So I conclude that an end node registered to a region will not be received in any other region. Hence, I register a new device to each region(US, EU, AU, RU etc) and then switch the credentials on the end-node dynamically.

I have now abandoned this repo in favour of a fork off the Semtech reference code which can be viewed here. https://github.com/ImperialSpaceSociety/LoRaMac-node. I needed to use the Non-volatile memory to store all the keys for an OTAA activation, to avoid repeated joins after resets and this later version of the stack has this functionality.  I am also getting the code to switch between the Things Network(ABP only) and The Helium Network(OTAA only) every 3 transmissions, to increase my coverage.

Below is a list of all my devices for each region.
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

pimente, 2021-09-28:
Thank you for the very thorough answer!

I am using the [mbed-os](https://os.mbed.com/mbed-os/) framework with [mbed studio IDE](https://os.mbed.com/studio/). A lot of different hardware is supported by [stm32customtargets](https://github.com/ARMmbed/stm32customtargets) and the example [mbed-os-example-lorawan](https://github.com/ARMmbed/mbed-os-example-lorawan) seemed much lighter than the Semtech LoRaWAN example which has a lot of boilerplate in my opinion. Not sure if mbed provides the same functionalities than the original Semtech code thought.

I did not know about the The Helium Network. It seems to have a great coverage. I now understand your need and reflexion around OTAA...
With your alternating transmission scheme, did you get a good sense of the Helium versus TTN coverage?
Does it really help to add the Helium Network?
If so, I'll give it a try.

From your screenshot, it seems that icspace26 is doing great with a flight longer than 110 days!? I can't wait for the flight report if you share it 😄

Cheers

MedadRufus, 2021-09-28:
>  With your alternating transmission scheme, did you get a good sense of the Helium versus TTN coverage?
I have yet to launch this tracker, with alternating helium/TTN transmissions. So I don't know. One think I have seen is the helium coverage is much better than TTN. Outside my house in London, UK, I immediately managed to successfully join the Helium network in a few minutes, using gateways nearby. On the Things Network, I have almost never gotten public gateways to pickup packets.

pimente, 2021-09-28:
> well ICSPACE26 is yet to be launched, only testing for 110 days 😄

Finger crossed! Do you plan to launch soon?

> I have looked very closely at the Semtech stack, and the only unnecessary part in there is the LoRaWAN Class B support, which I will never be using. Its not a big problem for me, as the compiled code size is 182 kb, less than the max of 192 kb for the STM32l072 processor I use. Ram is also under control, at around 11 kb, less than max of 20kb. I have chosen to use this stack because I know its well tested by the developers. I am less trusting of other ports of this code.

I agree that reliability is the most important criteria when using others' code for these flights. I've seen that your new fork introduces some UTs. That should help.

For the Helium Network, do you need multiple credentials for each region?
If not, and considering the coverage, I might move to the Helium Network instead of configuring TTN for each region...
Mbed implementation is lorawan 1.0.2. I see that you use version 1.0.3. Is it mandatory to connect to the Helium Network?

MedadRufus, 2021-09-28:
> For the Helium Network, do you need multiple credentials for each region?
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
MedadRufus, 2021-10-02:
One more thing to note: every time you do a join, a new dev_addr, NwkSKey, AppSKey are generated. The old ones may become invalid.

pimente, 2021-10-02:
The screenshot I have shared is a successful uplink just after the OTAA. I was suspecting from the Lora implementation's code that endianness was mixed up in the Helium console but the link you've shared just proves it. It is a bug in their interface.
The problem is that I have already tried with devaddr = 0x480002AC without success. I feel am missing something from your last discovery. Looking at the code, I don't see where AppEUI is being used with ABP. Have you understood that?

pimente, 2021-10-02:
I'll try again with devaddr = 0x480002AC just to make sure.

MedadRufus, 2021-10-02:
I have not looked closely at the implementation difference between OTAA /ABP in the Semtech reference code. However, I am sure the AppEUI is required for OTAA. So even when using ABP, i think the AppEui must be used somewhere.

MedadRufus, 2021-10-02:
Ill try will incorrect AppEUI and see if it will work.

MedadRufus, 2021-10-02:
Correction from me. I switched around a few bytes of my hard coded AppEUI, and it still works. This proves to me that actually, the AppEUI is not necessary. I think you caught it @pimente

MedadRufus, 2021-10-02:
The only keys that have to be correct I think are back to the `DevAddr`, `AppEUI` and `NwkSKey`. When I was testing yesterday, I keyed in the correct AppEUI, and immediately, it started working. It may have been some other cause that made it to work.

MedadRufus, 2021-10-02:
I would recommend trying with the Things Network first, as it is a lot more transparent. It shows the `DevAddr`(with correct endian), `NwkSKey` and `AppSKey` on the console. Then if it works, the move on to the Helium Network. It helps to have a gateway at hand to test with.

pimente, 2021-10-02:
This works for me as well! I suspect problem was coming from ADR but I still have to investigate this.
Switching to ABP, default DR was DR_5 which I though was not low enough to be received from the nearest gateway so I disabled ADR and tried different DR down to DR_0 without success.
Following our discussion, I joined again with OTAA, extracted DevAddr (watching out for the endianess), NwkSKey and AppSKey, reverted to all default parameters, so ADR as well and waited a bunch of uplinks on DR_5.
After 15, I got one which was received!

pimente, 2021-10-02:
These launches will happen before the end of the year for sure 😄

MedadRufus, 2021-10-02:
For a flying balloon, its best to disable ADR. ADR is useful if the device is static. It reduces the power level/air time to as low as possible, while maintaining the link.

pimente, 2021-10-02:
Yes, ADR was disabled for my last flight in September. In fact I was using BlindADR which was a success until Turkey where it lost coverage. We should make more tests to understand the limits of this hack on the Helium network. Does is work well with ADR disabled? Do the credential expire?... But this sounds like a huge step forward to achieve circumnavigation 👍

MedadRufus, 2021-10-02:
I have always disabled ADR, and had no problem.

I am putting my thoughts and plan B for the expiring credentials issue here. Its somewhat seperate from the current issue: https://github.com/ImperialSpaceSociety/LoRaMac-node/issues/214

pimente, 2021-10-02:
Yep, we've been quite of course the initial issue in this thread 😄
I'll make a new test now with ADR to try to discharge this problem.

MedadRufus, 2021-10-02:
I don't use ADR at all. I always use the highest possible power, and a fixed data rate. In the EU, I use DR_5 while in the rest of the world, I use DR_4. Note that in the US, the highest datarate is DR_4(not DR_5).

pimente, 2021-10-02:
Yes, I've seen your flight reports. Thks for sharing btw.
I've used DR_4 and DR_2 once every 10 uplinks. DR_4 was cleary not necessary over Europe and reducing my transmit frequency to respect the TTN fair policy. Now with Helium, since we are just bound by the official duty cycle (much better than TTN fair policy) and we pay per packet data size, not packet time, I have to think about what would is the next optimum...
If next tests proves this hack reliable, I will go full Helium I think.

pimente, 2021-10-02:
I confirm it works with ADR disabled. I must have been something else.

MedadRufus, 2021-10-02:
For testing purposes, if you are relying on public gateways for testing, your best chance of getting received is to set it to transmit at max power(TX_POWER_0) and at the lowest datarate(DR_0). IT makes a big difference.

But during flight you can increase datarate to DR_5. my 700 km transmission to the gateway on top of the alps was I think on DR_4.

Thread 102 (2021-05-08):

Lots of pointless downlinks

MedadRufus, 2021-05-08:
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

```json
{
  "name": "ns.mac.new_channel.request",
  "time": "2021-05-08T02:22:08.144659990Z",
  "identifiers": [
    {
      "device_ids": {
        "device_id": "icspace26-ttnv3-abp-eu-v1-0-3-1",
        "application_ids": {
          "application_id": "icss-lora-tracker"
        },
        "dev_addr": "260B7397"
      }
    }
  ],
  "data": {
    "@type": "type.googleapis.com/ttn.lorawan.v3.MACCommand.NewChannelReq",
    "channel_index": 5,
    "frequency": "867500000",
    "max_data_rate_index": 5
  },
  "correlation_ids": [
    "ns:downlink:01F54WGD8FDPS37XT14ARWHERP",
    "ns:uplink:01F54WGCVDXBCZ3GGC99YGF4W8",
    "pba:conn:up:01F4S0S1VDKJV6PHSBWY4PYEWG",
    "pba:uplink:01F54WGCQZMN8SDRXJ91HTHHRH",
    "rpc:/ttn.lorawan.v3.GsNs/HandleUplink:01F54WGCVDMMC5MC8HAW7PPWXF"
  ],
  "origin": "ip-10-100-5-72.eu-west-1.compute.internal",
  "context": {
    "tenant-id": "CgN0dG4="
  },
  "visibility": {
    "rights": [
      "RIGHT_APPLICATION_TRAFFIC_READ"
    ]
  },
  "unique_id": "01F54WGD8G8T2GAE6DA6QJ23WP"
}
```

MedadRufus, 2021-05-08:
Read this thread: https://www.thethingsnetwork.org/forum/t/is-v3-the-end-for-tinylora/43525/34?u=medadnewman

MedadRufus, 2021-05-09:
It could be that on device registration, the server txes on RX delay of 1 second, which is the LoRaWAN standard. I have by default changed the rx window to 5 seconds, hence the requests are not reaching the tracker.

It appears that only the first downlink message has to be sent after registration: the message to switch rx delay from 1 second to 5 seconds. The server just needs an ack, so it may be possible to do that on another device altogether and keep the rx delay to 5 seconds by default.

However, in other country settings(JP, US), it would be better to use the default settings. It appears that TTN does not change this rx delay for other countries, although it could just send up a message to tracker to switch it. Better to do it this way. There is no way I can receive this instruction to switch without an US/JP gateway, so let it just happen in the air as its meant to be.

MedadRufus, 2021-05-10:
Confirmed, using the default lorawan settings, where rx1 delay is 1 second, all the instructions are received.
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

MedadRufus, 2021-05-10:
After this first rx1 delay change request is made, it is never sent again. This is a problem on stateless machines, that do not store the fact that it rx1 delay is now 5 seconds, up from default 5. Same issue with setting data rate of RX2, which is by default DR0. The Things stack sends a request to swtich RX2 datarate to DR3, which is not saved either.

I think best solution is to hardcode these 2 settings for EU868 as default. The server can change that in the future if it wants, but at least it will be able to communicate with the tracker.

1. For other regions, I think we can ignore the statelessness. In the US, there is a chance of a successful downlink to tracker and subsequent ack that will satisfy the server, telling it that it has changed settings. However, the tracker will forget these settings.
The downside is rx1 will always be wrong on the tracker over the US, which means downlinks will never work.

2. But if we hardcode the rx1 delay to 5 seconds, the tracker will never receive the first switch command because that will be sent expecting rx1 delay of 1 second. One workaround is to acquire an US915 gateway, carry out the transaction under default settings(rx1 delay == 1 second) then hardcode RX1 delay to 5 seconds on the tracker.

3. Third solution is to set the rx 1 delay on the Things network app to 1 second during creation of the application. Then we will have no future problems. However, there are some known downsides of using rx 1, something todo with latency.

Solution 1 is worst, as we loose the downlink capablity forever. Solution 2 heavily depends on acquiring a US915 gateway, and legally transmitting on US frequencies. May not be feasible. Solution 3 is the most attractive, as the default  LoRaWAN settings are all used, and there is a good change it will work with the 1 second rx 1 delay, with slight performance decline.

MedadRufus, 2021-05-10:
I would say go for solution 3 for US, JP, AU but go for solution 2 for the EU.

In the EU, solution 2 can easily be carried out with a second end-node. Only risk is in the future, if rx1 delay is somehow changed from 5 to 1(lorawan default), then downlinks become impossible. What I am doing is not LoRaWAN compliant, which means I could endure future surprises if the things stack changes behaviour. But the change of this in the near term is very low.

The issue here is the statelessness of the tracker implementation in this repo. In the latest loramac-node releases(https://github.com/Lora-net/LoRaMac-node/releases/tag/v4.5.1), the settings are all saved to EEPROM. I don't think it is feasible to port over everything by launch this week.

MedadRufus, 2021-05-10:
For EU, maybe its better to just set the ttn settings to set to RX1 delay to 1 second, as before. no code changes at all, fully LoRaWAN default settings.

MedadRufus, 2021-06-15:
Occasionally, a

Closed 2021-09-25.

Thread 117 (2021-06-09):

On first transmisison after device creation, a whole bunch of pointless messages are sent down.

MedadRufus, 2021-06-09:
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
```

```

MedadRufus, 2021-06-09:
Problem is solved after one reset of tracker. Then normal transmissions resume.

MedadRufus, 2021-06-09:
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

MedadRufus, 2021-06-09:
This is the log from the terminal. Lots of stuff is being sent on port 2.
```
     put_in_power_save_mode carried out successfully!
                                                                     ================================================================
SENSOR AND GPS VALUES
================================================================
Temperature degrees C: 30.000000
Pressure mBar: 0.000000
Longitude: 0.000000 Latitude: 0.000000 altitude: 0
GPS time: 0
Solar voltage no load: 4
Solar voltage with GPS load: 4
Reset Count: 22
Data received from ground: 0
738000TX on freq 868100000 Hz at DR 5
ÿ 13s934ms: PHY txDone
ÿRX on freq 868100000 Hz at DR 5
ÿ 15s029ms: PHY rxDone
 15s062ms: APP> McpsConfirm STATUS: OK

 15s062ms: #= U/L FRAME 93 =# Class A, Port 99, data size 11, pwr 0, Channel Mask 00FF

 15s064ms: APP> MLMEInd STATUS: OK
TX on freq 867900000 Hz at DR 5
 15s138ms: APP> McpsInd STATUS: OK

 15s139ms: #= D/L FRAME 0 =# RxWin 1, Port 0, data size 0, rssi -89, snr 7

ÿ 15s206ms: PHY txDone
ÿÿRX on freq 867900000 Hz at DR 5
ÿ 20s236ms: PHY rxTimeOut
ÿRX on freq 869525000 Hz at DR 0
ÿ 21s438ms: PHY rxTimeOut
 21s465ms: APP> McpsConfirm STATUS: OK

 21s466ms: #= U/L FRAME 94 =# Class A, Port 2, data size 0, pwr 0, Channel Mask 00FF

 21s467ms: APP> MLMEInd STATUS: OK
TX on freq 868100000 Hz at DR 5
ÿ 21s588ms: PHY txDone
 21s589ms: APP> MLMEInd STATUS: OK
ÿRX on freq 868100000 Hz at DR 5
ÿ 26s619ms: PHY rxTimeOut
ÿRX on freq 869525000 Hz at DR 0
ÿ 27s821ms: PHY rxTimeOut
 27s848ms: APP> McpsConfirm STATUS: OK

 27s849ms: #= U/L FRAME 95 =# Class A, Port 2, data size 0, pwr 0, Channel Mask 00FF

 27s850ms: APP> MLMEInd STATUS: OK
TX on freq 867300000 Hz at DR 5
ÿ 27s970ms: PHY txDone
 27s971ms: APP> MLMEInd STATUS: OK
ÿÿRX on freq 867300000 Hz at DR 5
ÿ 33s000ms: PHY rxTimeOut
ÿRX on freq 869525000 Hz at DR 0
ÿ 34s203ms: PHY rxTimeOut
 34s230ms: APP> McpsConfirm STATUS: OK

 34s231ms: #= U/L FRAME 96 =# Class A, Port 2, data size 0, pwr 0, Channel Mask 00FF

 34s232ms: APP> MLMEInd STATUS: OK
TX on freq 868100000 Hz at DR 5
ÿ 34s353ms: PHY txDone
 34s354ms: APP> MLMEInd STATUS: OK
ÿÿRX on freq 868100000 Hz at DR 5
ÿ 39s383ms: PHY rxTimeOut
ÿRX on freq 869525000 Hz at DR 0
ÿ 40s585ms: PHY rxTimeOut
 40s613ms: APP> McpsConfirm STATUS: OK

 40s614ms: #= U/L FRAME 97 =# Class A, Port 2, data size 0, pwr 0, Channel Mask 00FF

 40s615ms: APP> MLMEInd STATUS: OK
TX on freq 868500000 Hz at DR 5
ÿ 40s736ms: PHY txDone
 40s737ms: APP> MLMEInd STATUS: OK
ÿRX on freq 868500000 Hz at DR 5
ÿ 45s766ms: PHY rxTimeOut
ÿRX on freq 869525000 Hz at DR 0
ÿ 46s968ms: PHY rxTimeOut
 46s996ms: APP> McpsConfirm STATUS: OK

 46s997ms: #= U/L FRAME 98 =# Class A, Port 2, data size 0, pwr 0, Channel Mask 00FF

 46s998ms: APP> MLMEInd STATUS: OK
TX on freq 867900000 Hz at DR 5
ÿ 47s119ms: PHY txDone
 47s120ms: APP> MLMEInd STATUS: OK
ÿÿRX on freq 867900000 Hz at DR 5
ÿ 52s149ms: PHY rxTimeOut
ÿRX on freq 869525000 Hz at DR 0
ÿ 53s351ms: PHY rxTimeOut
 53s378ms: APP> McpsConfirm STATUS: OK

 53s379ms: #= U/L FRAME 99 =# Class A, Port 2, data size 0, pwr 0, Channel Mask 00FF

 53s380ms: APP> MLMEInd STATUS: OK
TX on freq 868100000 Hz at DR 5
ÿ 53s501ms: PHY txDone
 53s502ms: APP> MLMEInd STATUS: OK
ÿREADING SENSOR AND GPS
temperature= 32,41 degrees C
***!!! Warning: put_in_continueous_mode failed !!!***
                                                     I2C not stuck low, carry on.
 I2C not stuck low, carry on.
                             Deinit i2c
                                       HAL_OK deinit
                                                    HAL_OK init
                                                               set setI2COutput carried out successfully!
                         The current dynamic model is INCORRECT. The current dynamic model is: 0
                Dynamic platform model changed successfully!
                                                             57s179ms: Fixtype: No fix  Sats:0  GPSfix_OK:0  GPS time: 18/10/2015, 00:00:01.0000  GPS Search time: 0.216 seconds
seconds since the Epoch: 1445126401
                                   RX on freq 868100000 Hz at DR 5
 58s531ms: PHY rxTimeOut
set setI2COutput carried out successfully!
                                          set setI2COutput carried out successfully!
    set GPS constellation only carried out successfully!
                                                        Dynamic platform model changed successfully!
                    set_powersave_config carried out successfully!
                                                                  put_in_power_save_mode carried out successfully!
                                  ================================================================
SENSOR AND GPS VALUES
================================================================
Temperature degrees C: 32.000000
Pressure mBar: 0.000000
Longitude: 0.000000 Latitude: 0.000000 altitude: 0
GPS time: 0
Solar voltage no load: 4
Solar voltage with GPS load: 4
Reset Count: 22
Data received from ground: 0
7380
    ÿRX on freq 869525000 Hz at DR 0
ÿ 59s734ms: PHY rxTimeOut
 59s761ms: APP> McpsConfirm STATUS: OK

 59s762ms: #= U/L FRAME 100 =# Class A, Port 99, data size 11, pwr 0, Channel Mask 00FF

 59s763ms: APP> MLMEInd STATUS: OK
TX on freq 867500000 Hz at DR 5
ÿ 59s884ms: PHY txDone
 59s885ms: APP> MLMEInd STATUS: OK
ÿRX on freq 867500000 Hz at DR 5
ÿ 64s915ms: PHY rxTimeOut
ÿRX on freq 869525000 Hz at DR 0
ÿ 66s117ms: PHY rxTimeOut
 66s144ms: APP> McpsConfirm STATUS: OK

 66s145ms: #= U/L FRAME 101 =# Class A, Port 2, data size 0, pwr 0, Channel Mask 00FF

 66s146ms: APP> MLMEInd STATUS: OK
TX on freq 867500000 Hz at DR 5
ÿ 66s267ms: PHY txDone
 66s268ms: APP> MLMEInd STATUS: OK
ÿÿRX on freq 867500000 Hz at DR 5
ÿ 71s297ms: PHY rxTimeOut
ÿRX on freq 869525000 Hz at DR 0
ÿ 72s500ms: PHY rxTimeOut
 72s527ms: APP> McpsConfirm STATUS: OK

 72s528ms: #= U/L FRAME 102 =# Class A, Port 2, data size 0, pwr 0, Channel Mask 00FF

 72s529ms: APP> MLMEInd STATUS: OK
TX on freq 867100000 Hz at DR 5
ÿ 72s650ms: PHY txDone
 72s651ms: APP> MLMEInd STATUS: OK
ÿRX on freq 867100000 Hz at DR 5
ÿ 77s680ms: PHY rxTimeOut
ÿÿRX on freq 869525000 Hz at DR 0
ÿ 78s882ms: PHY rxTimeOut
 78s910ms: APP> McpsConfirm STATUS: OK

 78s911ms: #= U/L FRAME 103 =# Class A, Port 2, data size 0, pwr 0, Channel Mask 00FF

 78s912ms: APP> MLMEInd STATUS: OK
TX on freq 867100000 Hz at DR 5
ÿ 79s033ms: PHY txDone
 79s034ms: APP> MLMEInd STATUS: OK
ÿRX on freq 867100000 Hz at DR 5
ÿ 84s036ms: PHY rxTimeOut
ÿRX on freq 869525000 Hz at DR 0
ÿ 85s265ms: PHY rxTimeOut
 85s292ms: APP> McpsConfirm STATUS: OK

 85s293ms: #= U/L FRAME 104 =# Class A, Port 2, data size 0, pwr 0, Channel Mask 00FF

 85s294ms: APP> MLMEInd STATUS: OK
TX on freq 868100000 Hz at DR 5
ÿ 85s416ms: PHY txDone
 85s416ms: APP> MLMEInd STATUS: OK
ÿÿRX on freq 868100000 Hz at DR 5
ÿ 90s446ms: PHY rxTimeOut
ÿRX on freq 869525000 Hz at DR 0
ÿ 91s648ms: PHY rxTimeOut
 91s675ms: APP> McpsConfirm STATUS: OK

 91s676ms: #= U/L FRAME 105 =# Class A, Port 2, data size 0, pwr 0, Channel Mask 00FF

 91s677ms: APP> MLMEInd STATUS: OK
TX on freq 868300000 Hz at DR 5
ÿ 91s798ms: PHY txDone
 91s799ms: APP> MLMEInd STATUS: OK
ÿRX on freq 868300000 Hz at DR 5
ÿ 96s829ms: PHY rxTimeOut
ÿRX on freq 869525000 Hz at DR 0
ÿ 98s031ms: PHY rxTimeOut
 98s058ms: APP> McpsConfirm STATUS: OK

 98s059ms: #= U/L FRAME 106 =# Class A, Port 2, data size 0, pwr 0, Channel Mask 00FF

 98s060ms: APP> MLMEInd STATUS: OK
TX on freq 867700000 Hz at DR 5
ÿ 98s180ms: PHY txDone
 98s181ms: APP> MLMEInd STATUS: OK
ÿÿREADING SENSOR AND GPS
temperature= 32,75 degrees C
***!!! Warning: put_in_continueous_mode failed !!!***
                                                     I2C not stuck low, carry on.
 I2C not stuck low, carry on.
                             Deinit i2c
                                       HAL_OK deinit
                                                    HAL_OK init
                                                               set setI2COutput carried out successfully!
                         The current dynamic model is INCORRECT. The current dynamic model is: 0
                Dynamic platform model changed successfully!
                                                            102s725ms: Fixtype: No fix  Sats:0  GPSfix_OK:0  GPS time: 18/10/2015, 00:00:01.0000  GPS Search time: 0.216 seconds
seconds since the Epoch: 1445126401
                                   RX on freq 867700000 Hz at DR 5
103s209ms: PHY rxTimeOut
RX on freq 869525000 Hz at DR 0
104s413ms: PHY rxTimeOut
set setI2COutput carried out successfully!
                                          set setI2COutput carried out successfully!
    set GPS constellation only carried out successfully!
                                                        Dynamic platform model changed successfully!
                    set_powersave_config carried out successfully!
                                                                  put_in_power_save_mode carried out successfully!
                                  ================================================================
SENSOR AND GPS VALUES
================================================================
Temperature degrees C: 32.000000
Pressure mBar: 0.000000
Longitude: 0.000000 Latitude: 0.000000 altitude: 0
GPS time: 0
Solar voltage no load: 4
Solar voltage with GPS load: 4
Reset Count: 22
Data received from ground: 0
7380
    104s916ms: APP> McpsConfirm STATUS: OK

104s917ms: #= U/L FRAME 107 =# Class A, Port 99, data size 11, pwr 0, Channel Mask 00FF TX on freq 868100000 Hz at DR 5
ÿ105s040ms: PHY txDone
105s041ms: APP> MLMEInd STATUS: OK
ÿÿRX on freq 868100000 Hz at DR 5
ÿ110s070ms: PHY rxTimeOut
ÿRX on freq 869525000 Hz at DR 0
ÿ111s272ms: PHY rxTimeOut
111s299ms: APP> McpsConfirm STATUS: OK

111s300ms: #= U/L FRAME 108 =# Class A, Port 2, data size 0, pwr 0, Channel Mask 00FF

111s301ms: APP> MLMEInd STATUS: OK
TX on freq 867300000 Hz at DR 5
ÿ111s422ms: PHY txDone
111s423ms: APP> MLMEInd STATUS: OK
ÿRX on freq 867300000 Hz at DR 5
ÿ116s453ms: PHY rxTimeOut
ÿRX on freq 869525000 Hz at DR 0
ÿ117s655ms: PHY rxTimeOut
117s682ms: APP> McpsConfirm STATUS: OK

117s683ms: #= U/L FRAME 109 =# Class A, Port 2, data size 0, pwr 0, Channel Mask 00FF

117s684ms: APP> MLMEInd STATUS: OK
TX on freq 867700000 Hz at DR 5
ÿ117s805ms: PHY txDone
117s806ms: APP> MLMEInd STATUS: OK
ÿÿRX on freq 867700000 Hz at DR 5
ÿ122s835ms: PHY rxTimeOut
ÿRX on freq 869525000 Hz at DR 0
ÿ124s038ms: PHY rxTimeOut
124s065ms: APP> McpsConfirm STATUS: OK

124s066ms: #= U/L FRAME 110 =# Class A, Port 2, data size 0, pwr 0, Channel Mask 00FF

124s067ms: APP> MLMEInd STATUS: OK
TX on freq 868500000 Hz at DR 5
ÿ124s188ms: PHY txDone
124s189ms: APP> MLMEInd STATUS: OK
ÿÿRX on freq 868500000 Hz at DR 5
ÿ129s218ms: PHY rxTimeOut
ÿRX on freq 869525000 Hz at DR 0
ÿ130s811ms: PHY rxTimeOut
130s838ms: APP> McpsConfirm STATUS: OK

130s839ms: #= U/L FRAME 111 =# Class A, Port 2, data size 0, pwr 0, Channel Mask 00FF

130s840ms: APP> MLMEInd STATUS: OK
TX on freq 867300000 Hz at DR 5
ÿ130s961ms: PHY txDone
130s962ms: APP> MLMEInd STATUS: OK
ÿRX on freq 867300000 Hz at DR 5
ÿ135s992ms: PHY rxTimeOut
ÿRX on freq 869525000 Hz at DR 0
ÿ137s194ms: PHY rxTimeOut
137s221ms: APP> McpsConfirm STATUS: OK

137s222ms: #= U/L FRAME 112 =# Class A, Port 2, data size 0, pwr 0, Channel Mask 00FF
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

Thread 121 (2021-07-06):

Startup is stuck at HW_RTC_INIT()

MedadRufus, 2021-07-06:
I have seen it never recover, getting stuck permenantly. Not sure if its hardware issue. Ensure HW watchdog can deal with this.

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

MedadRufus, 2021-07-06:
Its intermittent though.

MedadRufus, 2021-07-06:
Stuck here:
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

MedadRufus, 2021-07-06:
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

MedadRufus, 2021-07-06:
Hardware watchdog reset is not sufficient to reset. It is going continueous reset after getting stuck at this point.
Looks to me that the RTC is not starting up.

Closed 2021-09-25.

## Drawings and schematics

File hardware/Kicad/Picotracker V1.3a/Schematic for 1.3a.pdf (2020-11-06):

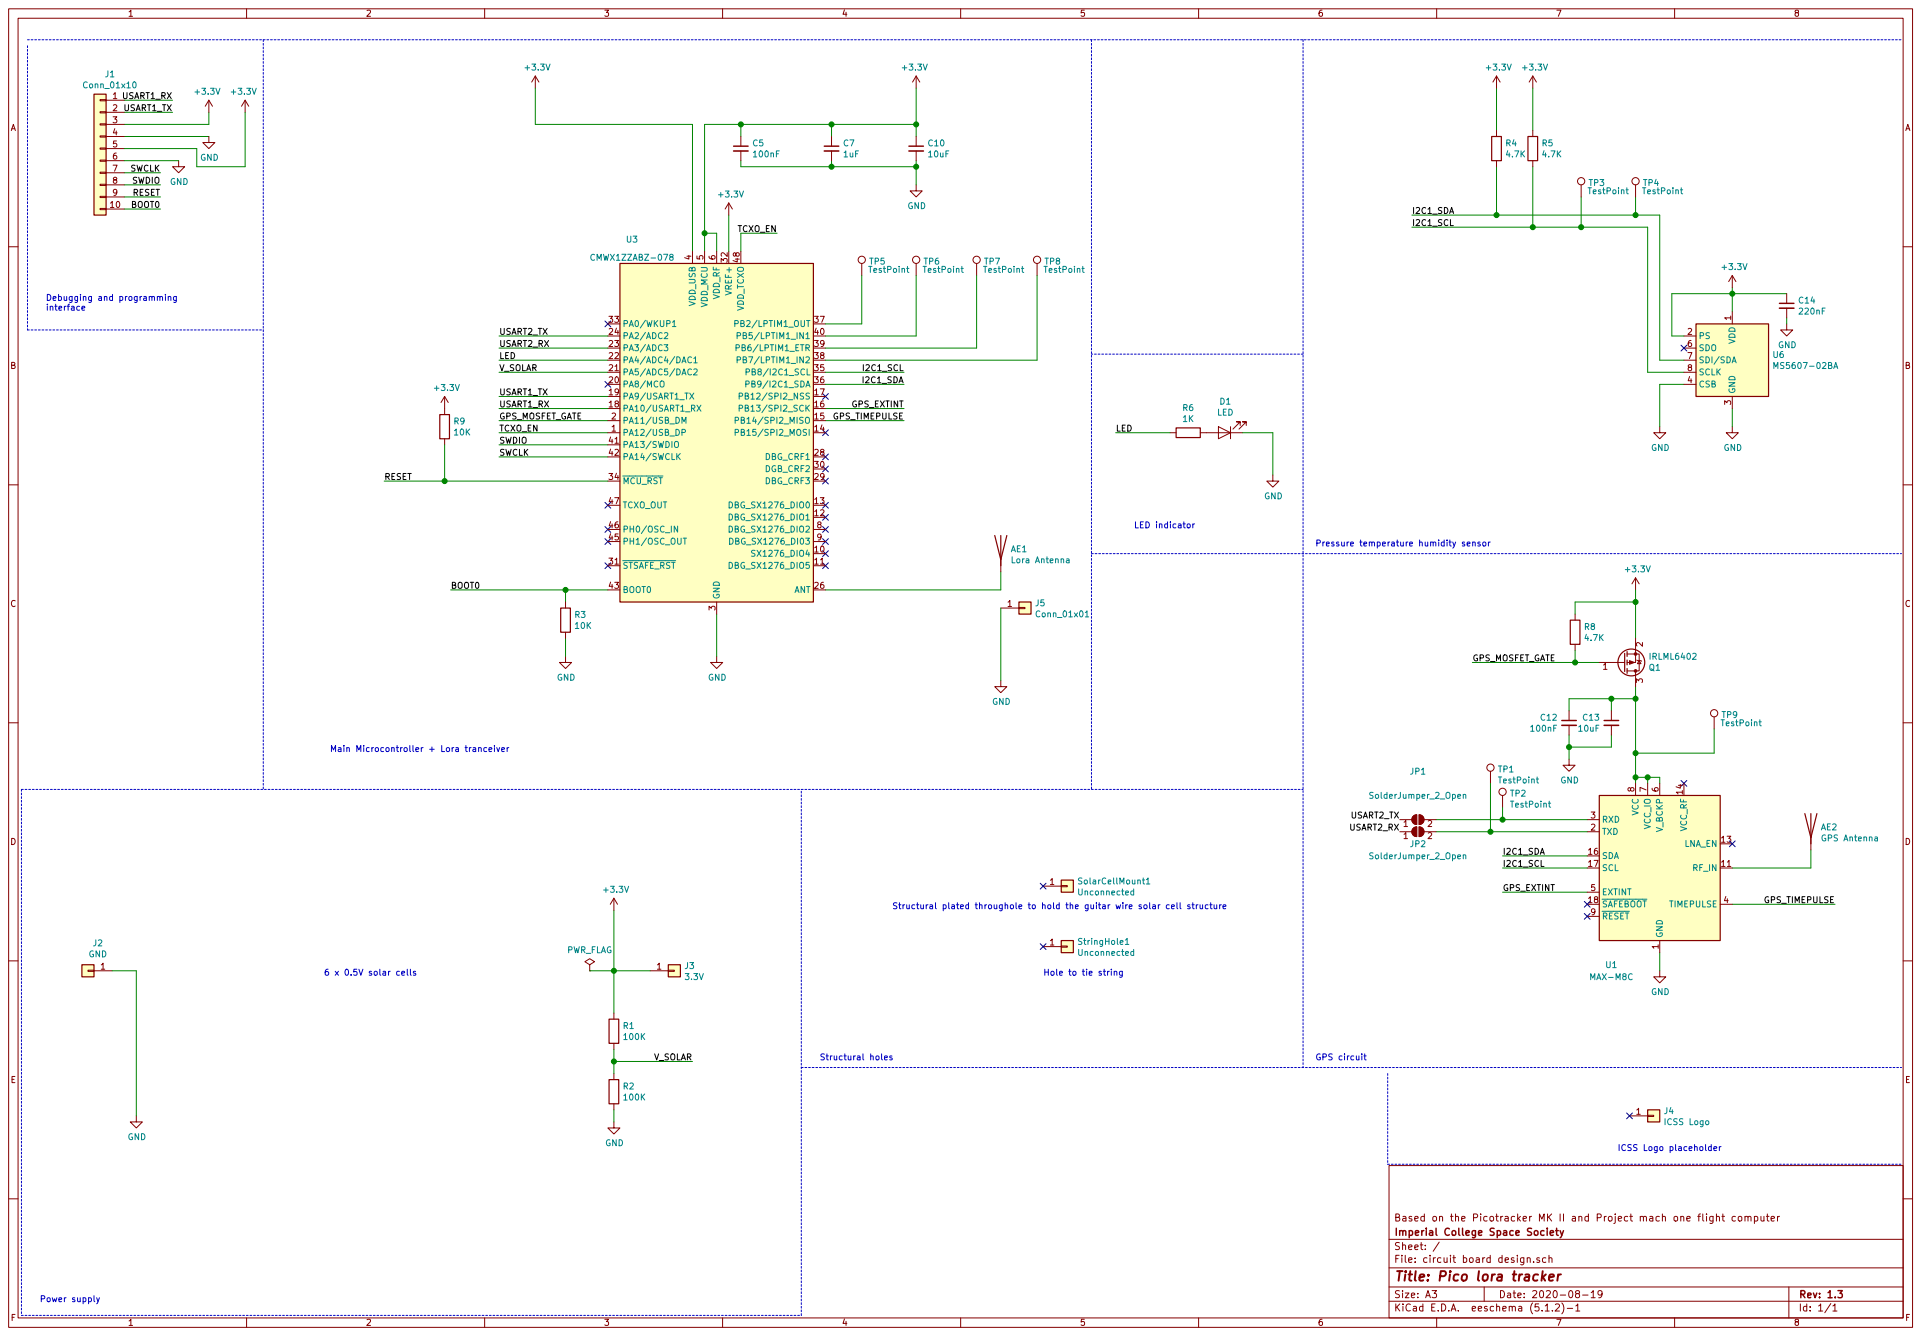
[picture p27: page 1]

Pressure temperature humidity sensor GPS circuit Power supply

Based on the Picotracker MK II and Project mach one flight computer
Imperial College Space Society
File: circuit board design.sch Sheet: /
Id: 1/1 Title: Pico lora tracker

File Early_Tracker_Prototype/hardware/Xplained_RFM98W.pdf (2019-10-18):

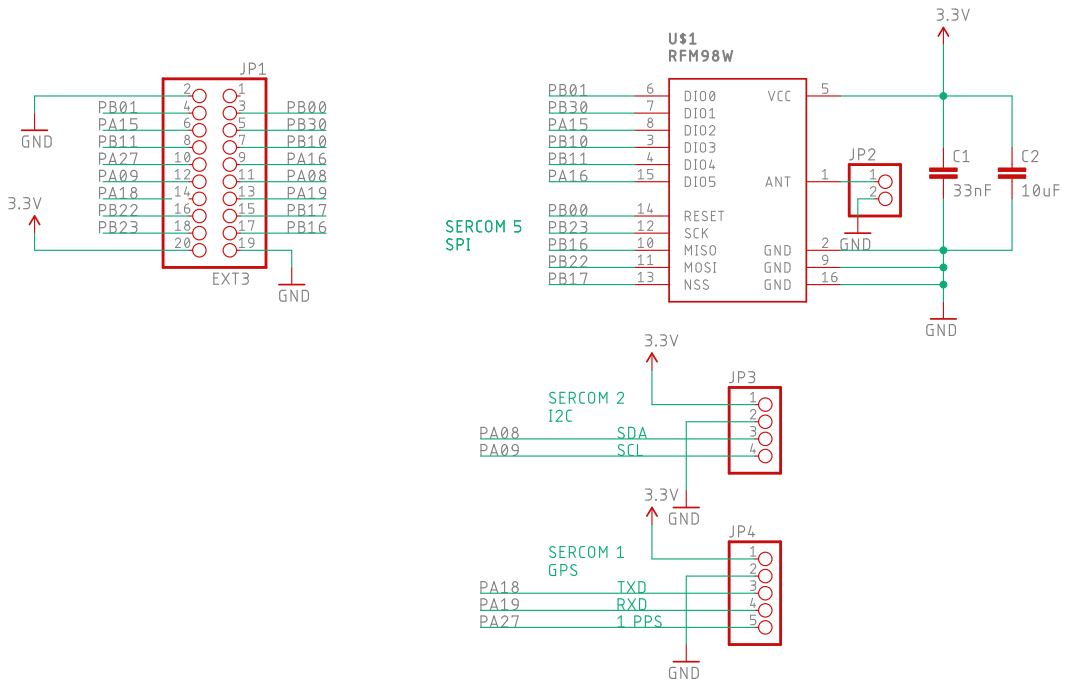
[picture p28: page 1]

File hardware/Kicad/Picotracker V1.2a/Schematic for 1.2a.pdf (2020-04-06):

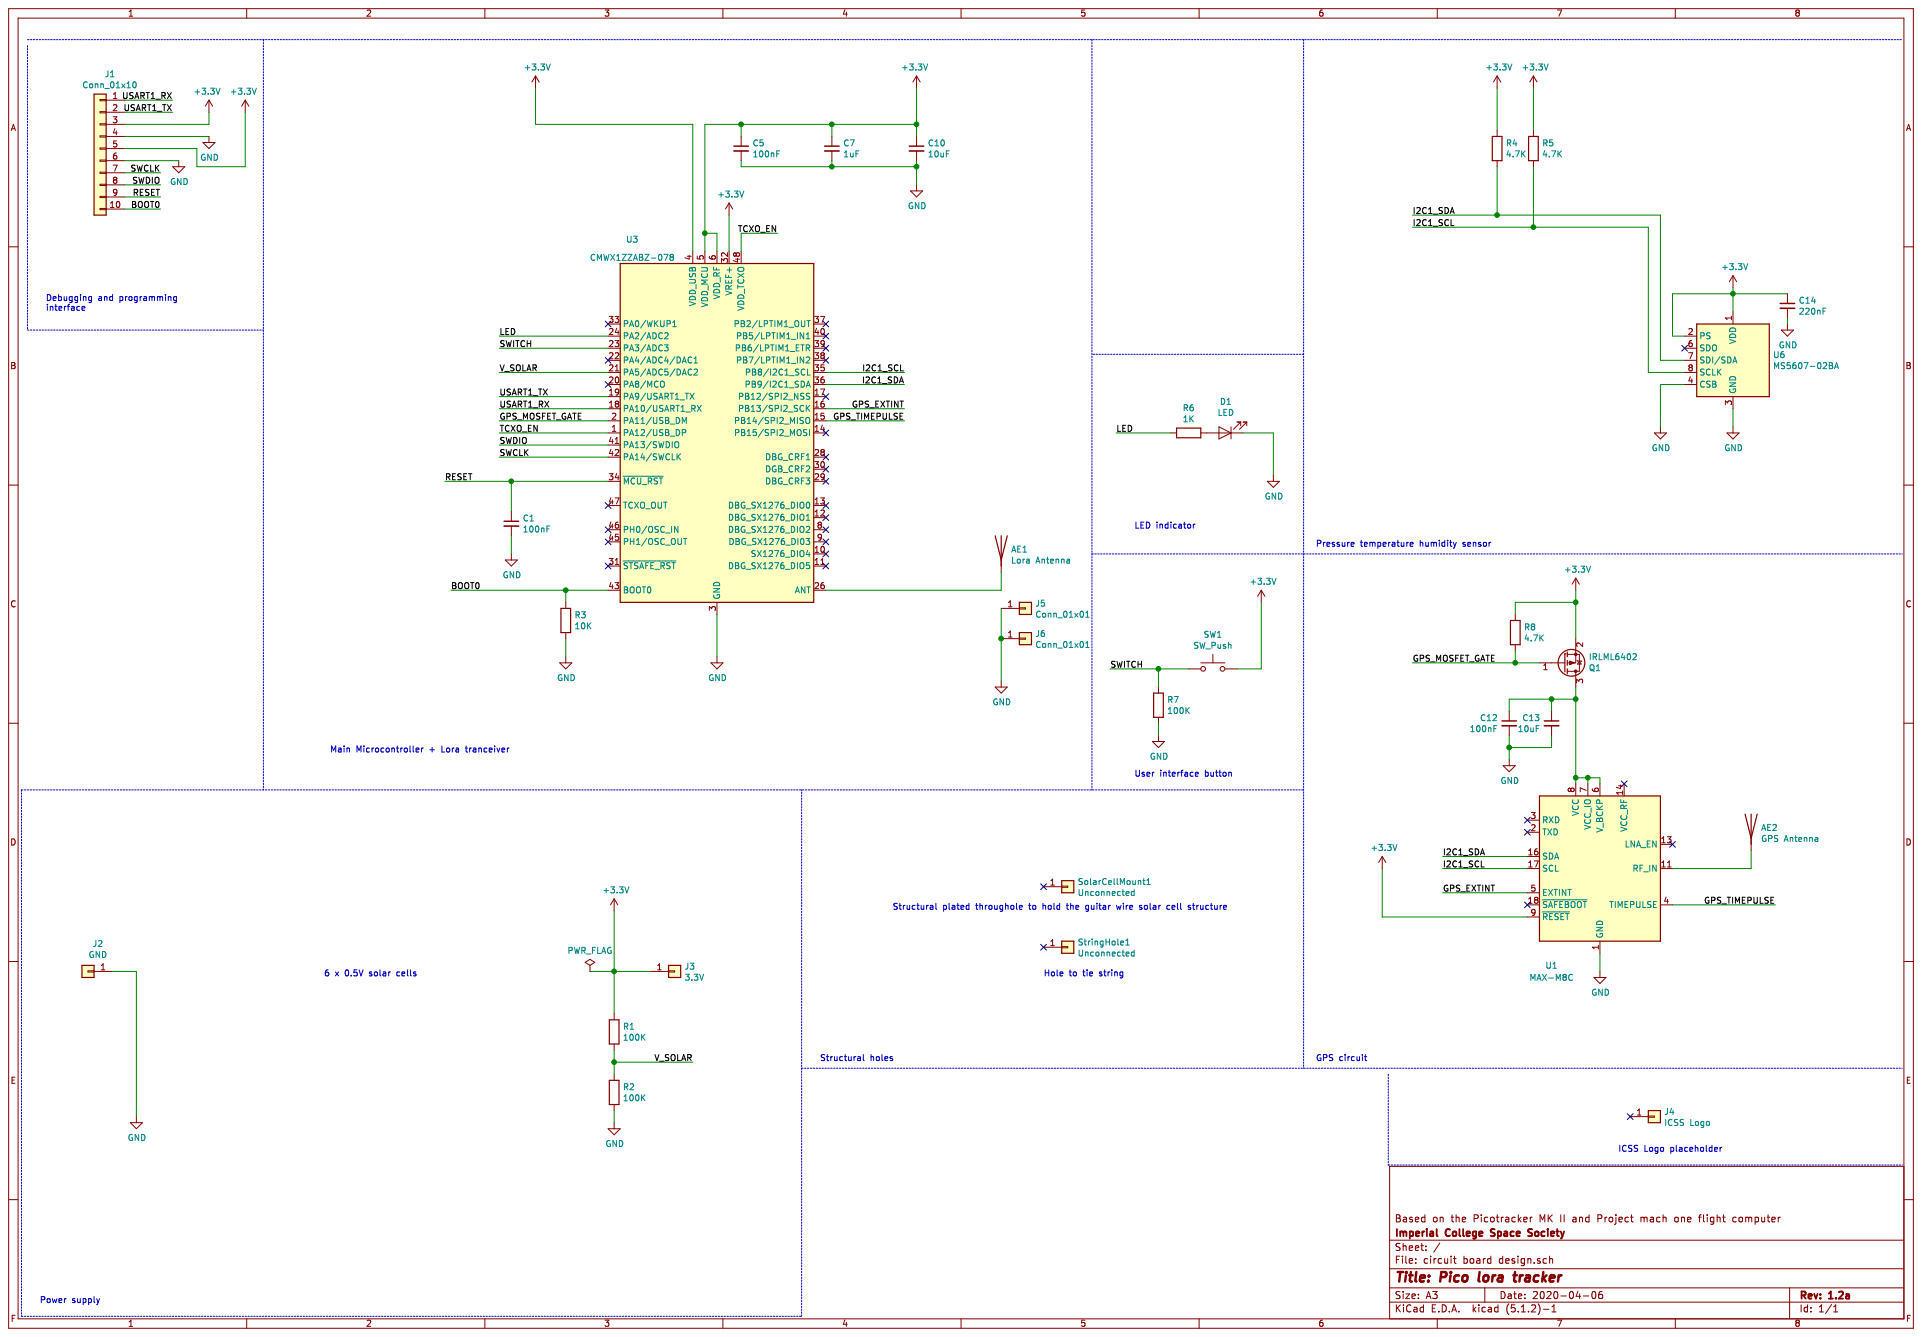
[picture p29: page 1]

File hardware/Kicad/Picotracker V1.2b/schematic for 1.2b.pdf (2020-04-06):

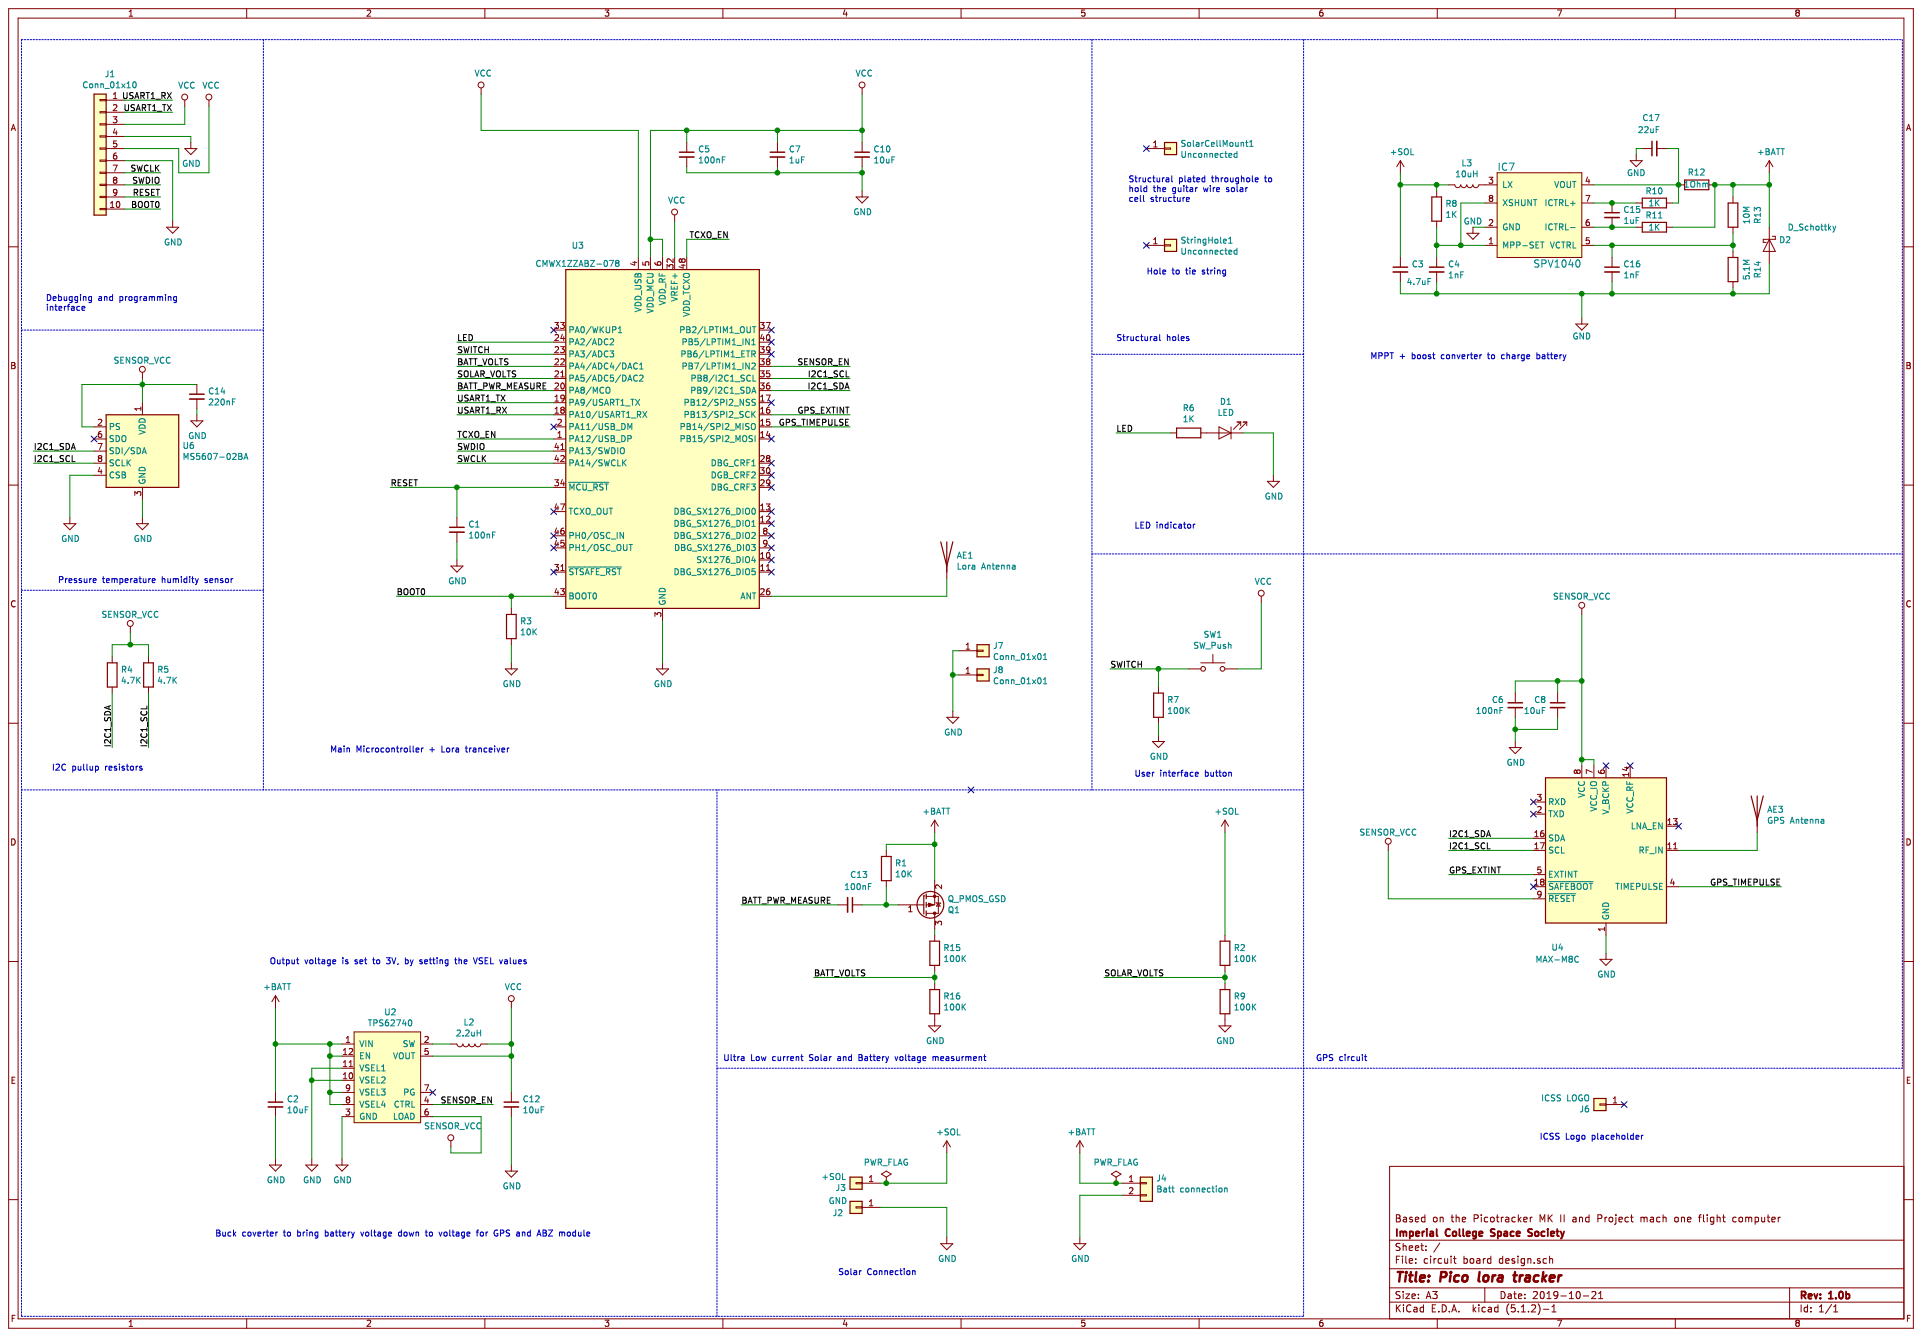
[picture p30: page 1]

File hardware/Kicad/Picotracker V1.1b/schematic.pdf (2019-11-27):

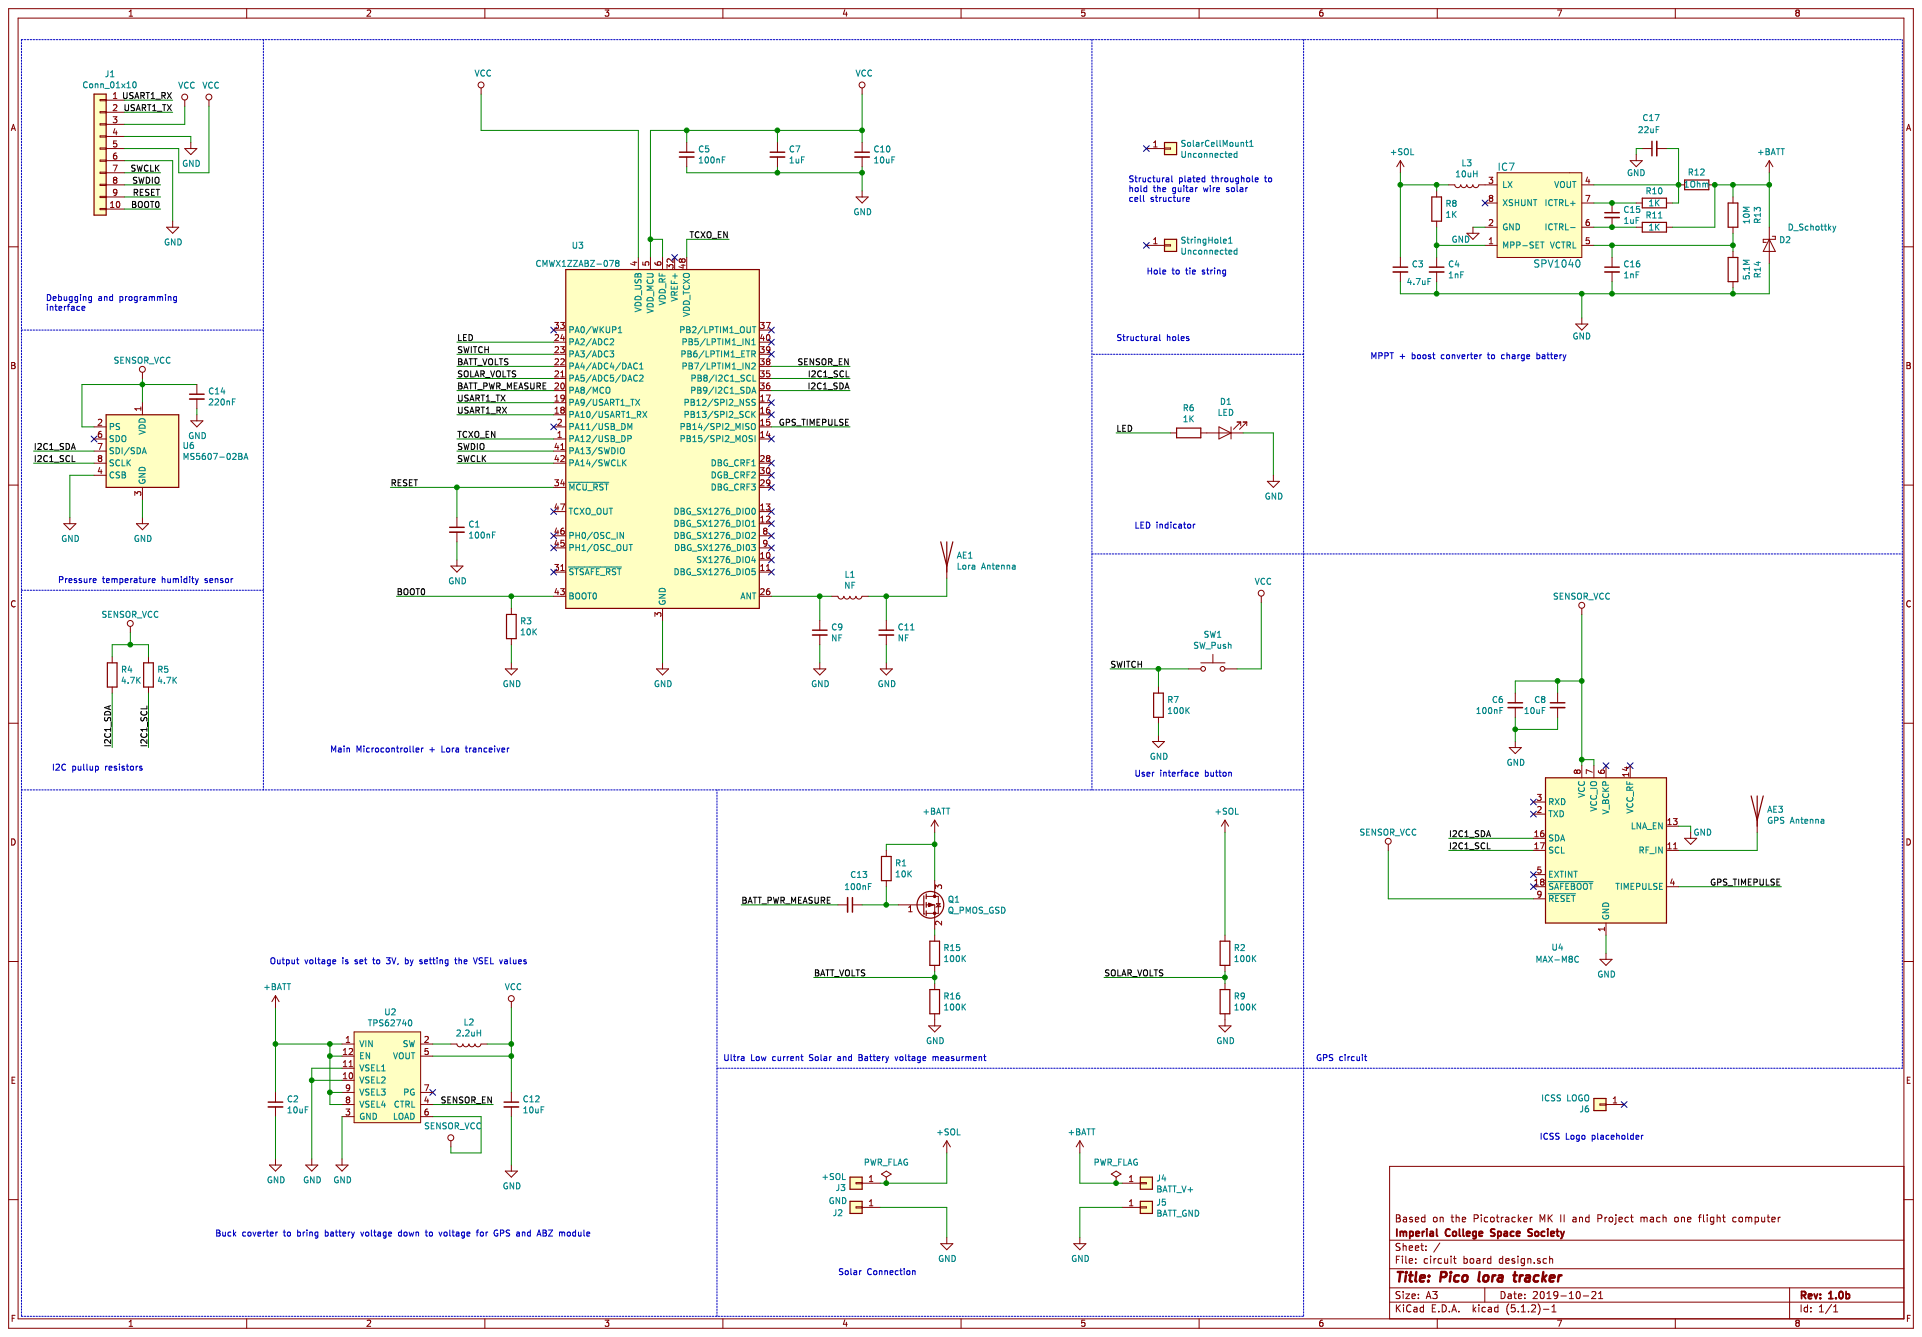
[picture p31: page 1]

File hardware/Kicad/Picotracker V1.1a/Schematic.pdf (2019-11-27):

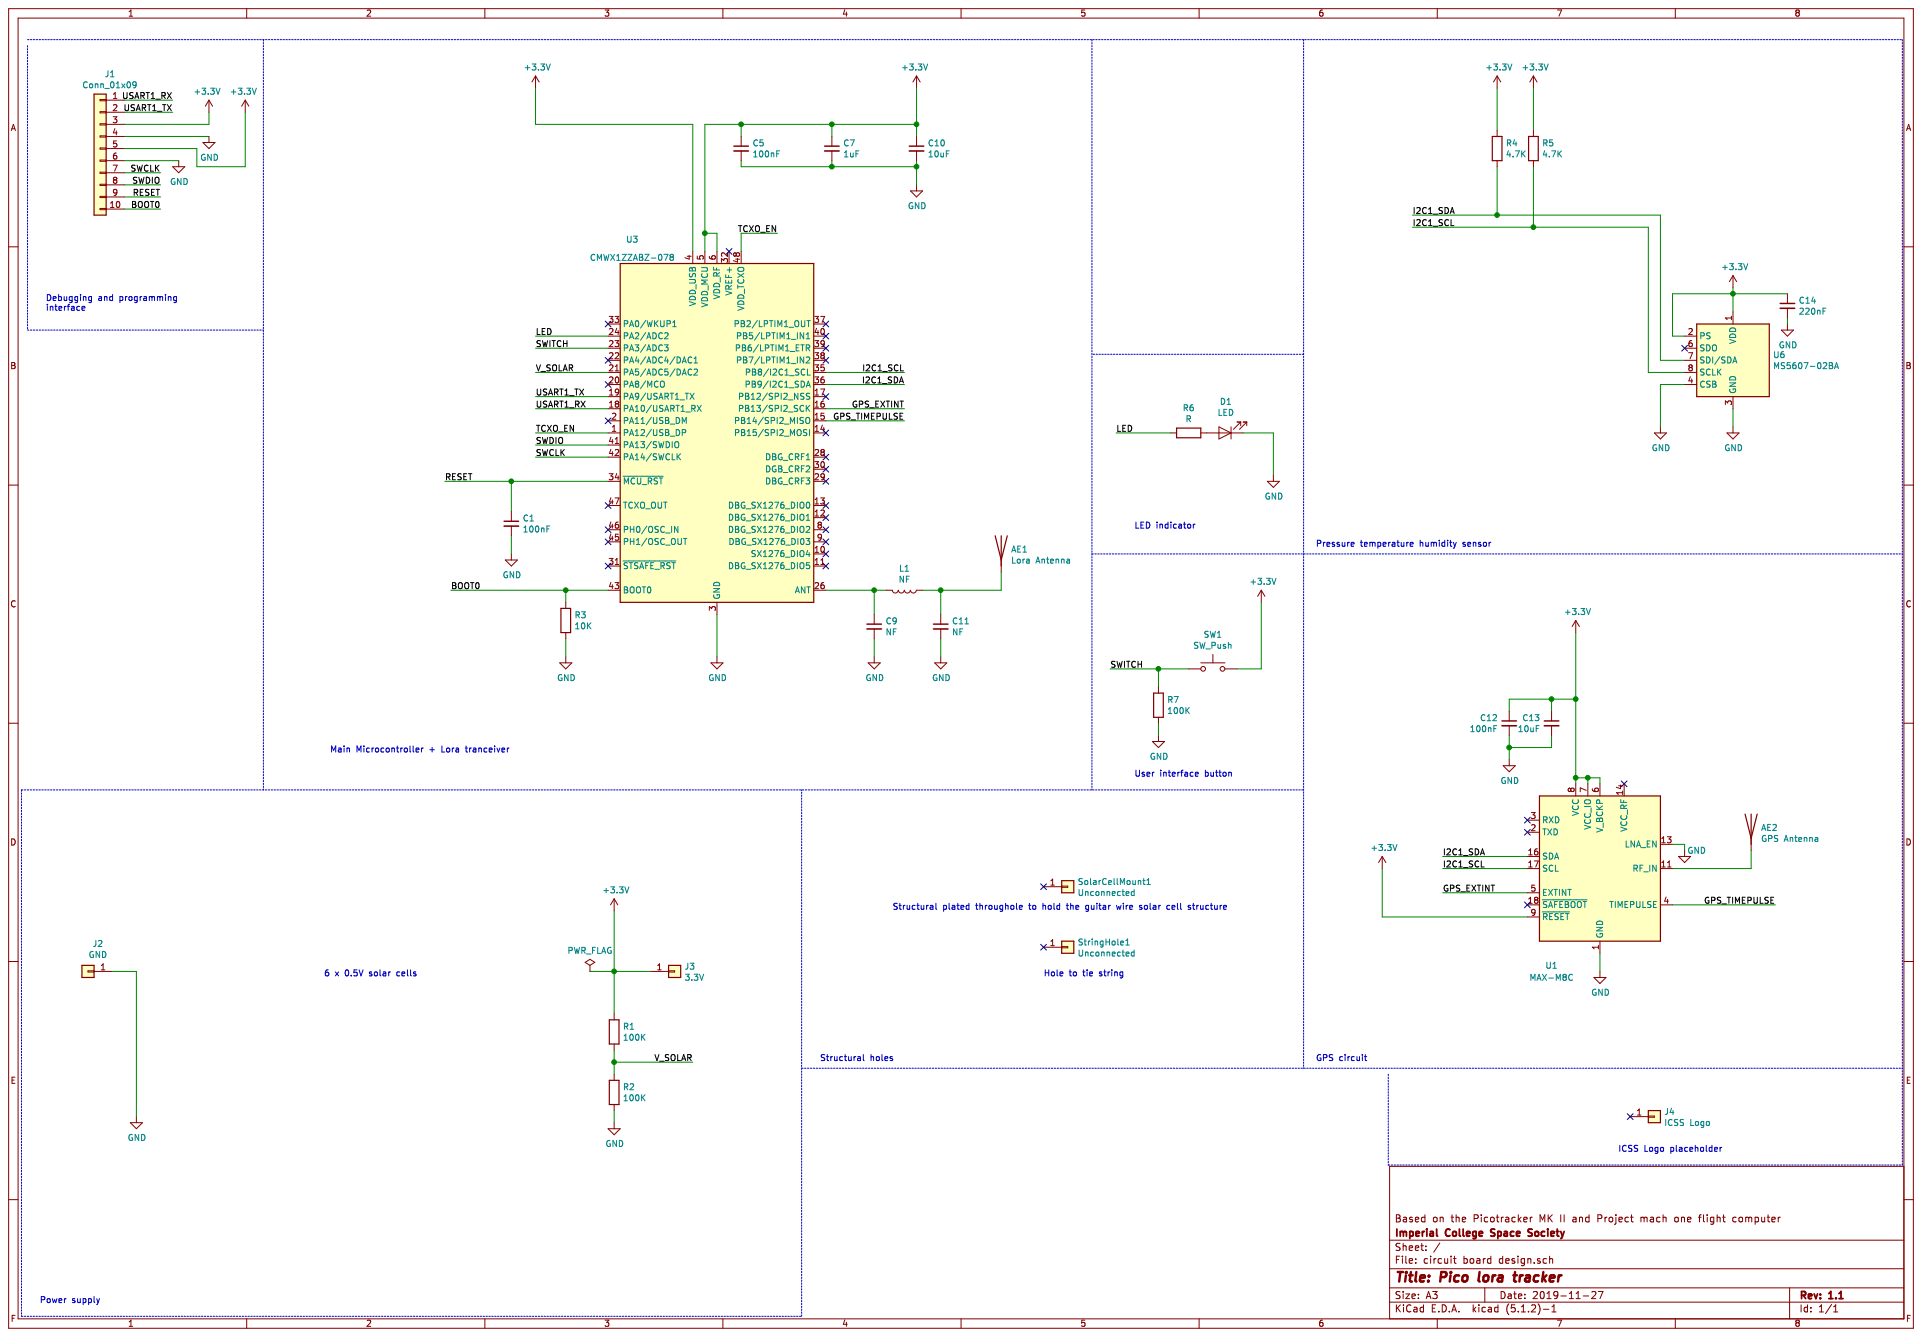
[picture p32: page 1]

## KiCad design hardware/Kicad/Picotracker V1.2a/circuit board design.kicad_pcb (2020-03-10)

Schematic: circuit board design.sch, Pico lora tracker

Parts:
AE1: Lora Antenna; SolderWirePad_1x01_Drill0.8mm
AE2: GPS Antenna; SolderWirePad_1x01_Drill0.8mm
C1, C5, C12: 100nF; C_0402_1005Metric
C7: 1uF; C_0603_1608Metric
C10, C13: 10uF; C_0603_1608Metric
C14: 220nF; C_0603_1608Metric
D1: LED; LED_0402_1005Metric
J1: Conn_01x10; 10Pad
J2: GND; SolderWirePad_1x01_Drill0.8mm
J3: 3.3V; SolderWirePad_1x01_Drill0.8mm
J4: ICSS Logo; ICSS_Logo
J5, J6: Conn_01x01; SolderWirePad_1x01_Drill0.8mm
Q1: IRLML6402; SOT-23
R1, R2, R7: 100K; R_0402_1005Metric
R3: 10K; R_0402_1005Metric
R4, R5, R8: 4.7K; R_0402_1005Metric
R6: 1K; R_0402_1005Metric
SW1: SW_Push; EVPAWCD4A
SolarCellMount1: Unconnected; SolderWirePad_1x01_Drill0.8mm
StringHole1: Unconnected; SolderWirePad_1x01_Drill0.8mm
U1: MAX-M8C; ublox_MAX
U3: CMWX1ZZABZ-078; CMWX1ZZABZ
U6: MS5607-02BA; LGA-8_3x5mm_P1.25mm

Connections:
+3V3: C5.1, C7.1, C10.1, C14.1, J1.3, J1.5, J3.1, Q1.2 (S), R1.1, R4.1, R5.1, R8.1, SW1.2, U1.9 (~RESET), U3.4 (VDD_USB), U3.5 (VDD_MCU), U3.6 (VDD_RF), U3.32 (VREF+), U6.1 (VDD), U6.2 (PS)
/BOOT0: J1.10, R3.1, U3.43 (BOOT0)
/GPS_EXTINT: U1.5 (EXTINT), U3.16 (PB13/SPI2_SCK)
/GPS_MOSFET_GATE: Q1.1 (G), R8.2, U3.2 (PA11/USB_DM)
/GPS_TIMEPULSE: U1.4 (TIMEPULSE), U3.15 (PB14/SPI2_MISO)
/I2C1_SCL: R5.2, U1.17 (SCL), U3.35 (PB8/I2C1_SCL), U6.8 (SCLK)
/I2C1_SDA: R4.2, U1.16 (SDA), U3.36 (PB9/I2C1_SDA), U6.7 (SDI/SDA)
/LED: R6.2, U3.24 (PA2/ADC2)
/RESET: C1.1, J1.9, U3.34 (~MCU_RST)
/SWCLK: J1.7, U3.42 (PA14/SWCLK)
/SWDIO: J1.8, U3.41 (PA13/SWDIO)
/SWITCH: R7.1, SW1.1, U3.23 (PA3/ADC3)
/TCXO_EN: U3.1 (PA12/USB_DP), U3.48 (VDD_TCXO)
/USART1_RX: J1.1, U3.18 (PA10/USART1_RX)
/USART1_TX: J1.2, U3.19 (PA9/USART1_TX)
/V_SOLAR: R1.2, R2.1, U3.21 (PA5/ADC5/DAC2)
GND: C1.2, C5.2, C7.2, C10.2, C12.2, C13.2, C14.2, D1.1 (K), J1.4, J1.6, J2.1, J5.1, J6.1, R2.2, R3.2, R7.2, U1.1 (GND), U1.10 (GND), U1.12 (GND), U3.3 (GND), U3.7 (GND), U3.25 (GND), U3.27 (GND), U3.44 (GND), U3.49 (GND), U3.50 (GND), U3.51 (GND), U3.52 (GND), U3.53 (GND), U3.54 (GND), U3.55 (GND), U3.56 (GND), U3.57 (GND), U6.3 (GND), U6.4 (CSB), U6.5 (CSB)
unnamed: AE1.1, U3.26 (ANT)
unnamed: AE2.1, U1.11 (RF_IN)
unnamed: C12.1, C13.1, Q1.3 (D), U1.6 (V_BCKP), U1.7 (VCC_IO), U1.8 (VCC)
unnamed: D1.2 (A), R6.1

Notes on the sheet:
Debugging and programming interface
Pressure temperature humidity sensor
GPS circuit
Power supply
6 x 0.5V solar cells
Main Microcontroller + Lora tranceiver
Structural plated throughole to hold the guitar wire solar cell structure
User interface button
LED indicator
Hole to tie string
Structural holes
ICSS Logo placeholder

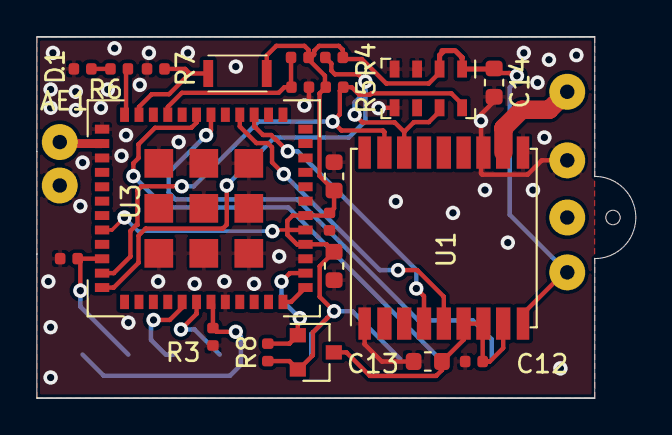
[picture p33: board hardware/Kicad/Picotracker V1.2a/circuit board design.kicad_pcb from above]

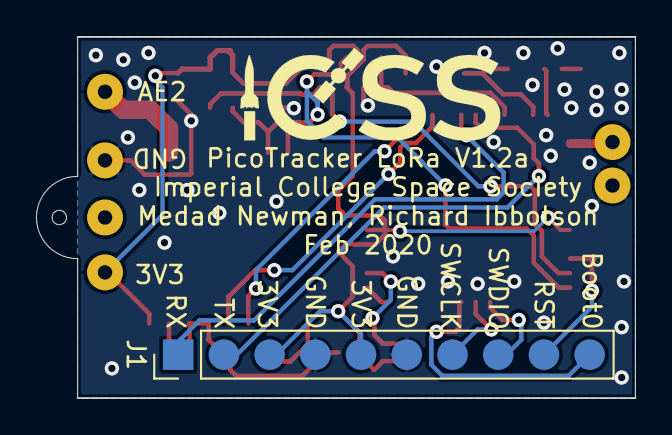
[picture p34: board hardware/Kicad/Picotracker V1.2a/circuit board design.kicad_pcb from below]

Board: 2 copper layers, 33.3 x 20.1 mm, 30 parts (2 on the bottom side), 21 nets.

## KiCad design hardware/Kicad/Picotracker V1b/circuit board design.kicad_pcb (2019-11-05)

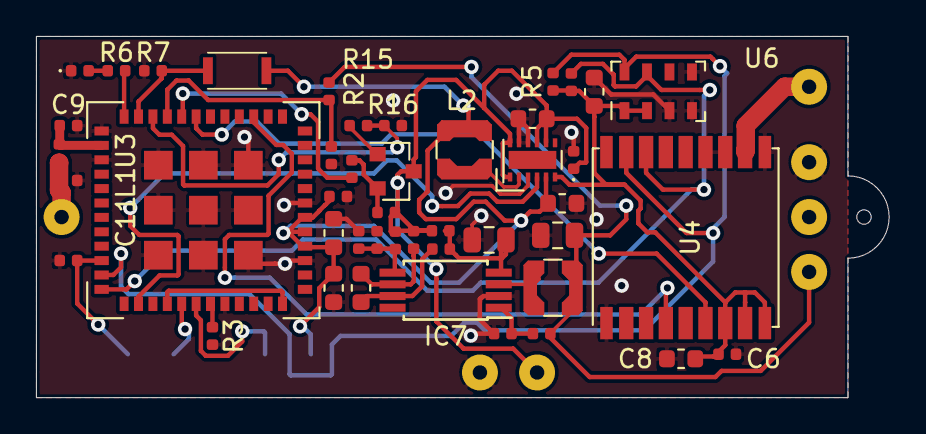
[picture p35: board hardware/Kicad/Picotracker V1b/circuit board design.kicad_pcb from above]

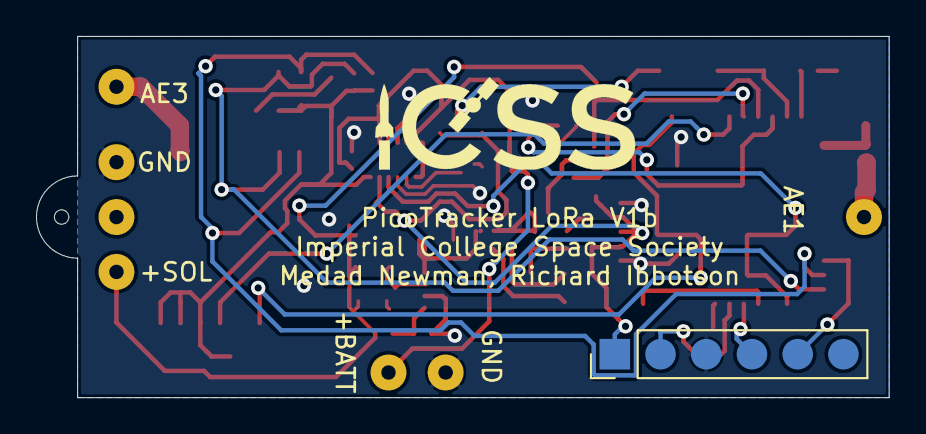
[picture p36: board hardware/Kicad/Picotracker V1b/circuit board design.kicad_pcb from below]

Board: 2 copper layers, 47.4 x 20.1 mm, 55 parts (8 on the bottom side), 33 nets.

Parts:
+BATT: BATT_V+; SolderWirePad_1x01_Drill0.8mm
+SOL: +SOL; SolderWirePad_1x01_Drill0.8mm
AE1: Lora Antenna; SolderWirePad_1x01_Drill0.8mm
AE3: GPS Antenna; SolderWirePad_1x01_Drill0.8mm
C1, C5, C6, C13: 100nF; C_0402_1005Metric
C2, C8, C10, C12: 10uF; C_0603_1608Metric
C3: 4.7uF; C_0805_2012Metric
C4, C16: 1nF; C_0402_1005Metric
C7, C15: 1uF; C_0603_1608Metric
C9, C11: NF; C_0402_1005Metric
C14: 220nF; C_0603_1608Metric
C17: 22uF; C_0805_2012Metric
D1: LED; LED_0402_1005Metric
D2: D_Schottky; D_0402_1005Metric
GND: BATT_GND; SolderWirePad_1x01_Drill0.8mm
GND#2: GND; SolderWirePad_1x01_Drill0.8mm
IC7: SPV1040; TSSOP-8_4.4x3mm_P0.65mm
J1: Conn_01x06; special_test_pads
J6: ICSS LOGO; ICSS_Logo
L1: NF; C_0402_1005Metric
L2: 2.2uH; L_Coilcraft_LPS3015
L3: 10uH; L_Coilcraft_LPS3015
Q1: Q_PMOS_DGS; SOT-23
R1, R3: 10K; R_0402_1005Metric
R2, R7, R9, R15, R16: 100K; R_0402_1005Metric
R4, R5: 4.7K; R_0402_1005Metric
R6: R; R_0402_1005Metric
R8, R10, R11: 1K; R_0402_1005Metric
R12: 1Ohm; R_0402_1005Metric
R13: 10M; R_0402_1005Metric
R14: 5.1M; R_0402_1005Metric
SW1: SW_Push; EVPAWCD4A
SolarCellMount1: Unconnected; SolderWirePad_1x01_Drill0.8mm
StringHole1: Unconnected; SolderWirePad_1x01_Drill0.8mm
U2: TPS62740; WSON-12-1EP_3x2mm_P0.5mm_EP1x2.65
U3: CMWX1ZZABZ-078; CMWX1ZZABZ
U4: MAX-M8C; ublox_MAX
U6: MS5607-02BA; LGA-8_3x5mm_P1.25mm

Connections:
+BATT: +BATT.1, C2.1, D2.1, Q1.3, R1.1, R11.1, R12.2, R13.2, U2.1, U2.8, U2.9, U2.12
+SOL: +SOL.1, C3.1, L3.2, R2.1, R8.1
/BATT_PWR_MEASURE: C13.2, U3.20
/BATT_VOLTS: R15.2, R16.1, U3.22
/GPS_BCKP: U3.19, U4.6
/GPS_TIMEPULSE: U3.15, U4.4
/I2C1_SCL: R5.2, U3.35, U4.17, U6.8
/I2C1_SDA: R4.2, U3.36, U4.16, U6.7
/LED: R6.2, U3.24
/RESET: C1.1, J1.5, U3.34
/SENSOR_EN: U2.4, U3.38
/SOLAR_VOLTS: R2.2, R9.1, U3.21
/SWCLK: J1.2, U3.42
/SWDIO: J1.4, U3.41
/SWITCH: R7.1, SW1.1, U3.23
/TCXO_EN: U3.40, U3.48
GND: C1.2, C2.2, C3.2, C4.2, C5.2, C6.2, C7.2, C8.2, C9.2, C10.2, C11.2, C12.2, C14.2, C16.2, C17.1, D1.1, D2.2, GND.1, GND#2.1, IC7.2, J1.3, R3.2, R7.2, R9.2, R14.1, R16.2, U2.3, U2.10, U2.11, U3.3, U3.7, U3.25, U3.27, U3.44, U3.49, U3.50, U3.51, U3.52, U3.53, U3.54, U3.55, U3.56, U3.57, U4.1, U4.10, U4.12, U4.13, U6.3, U6.4, U6.5
unnamed: AE1.1, C11.1, L1.1
unnamed: AE3.1, U4.11
unnamed: C4.1, IC7.1, R8.2
unnamed: C9.1, L1.2, U3.26
unnamed: C13.1, Q1.2, R1.2
unnamed: C15.1, IC7.7, R10.2
unnamed: C15.2, IC7.6, R11.2
unnamed: C16.1, IC7.5, R13.1, R14.2
unnamed: C17.2, IC7.4, R10.1, R12.1
unnamed: D1.2, R6.1
unnamed: IC7.3, L3.1
unnamed: L2.2, U2.2
unnamed: Q1.1, R15.1
unnamed: R3.1, U3.43
SENSOR_VCC: C6.1, C8.1, C14.1, R4.1, R5.1, U2.6, U4.7, U4.8, U4.9, U6.1, U6.2
VCC: C5.1, C7.1, C10.1, C12.1, J1.1, L2.1, SW1.2, U2.5, U3.4, U3.5, U3.6

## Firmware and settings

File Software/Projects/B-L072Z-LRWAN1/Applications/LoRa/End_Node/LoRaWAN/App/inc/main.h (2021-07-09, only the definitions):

#define GPS_PPS_Pin GPIO_PIN_14
#define GPS_PPS_GPIO_Port GPIOB
#define GPS_INT_Pin GPIO_PIN_13
#define GPS_INT_GPIO_Port GPIOB
#define SENSOR_EN_PIN GPIO_PIN_7
#define SENSOR_EN_GPIO_Port GPIOB
#define GPS_EN_PIN GPIO_PIN_11
#define GPS_EN_GPIO_Port GPIOA
#define SENSOR_ENABLED 0                    /* Enable ms5607 sensor. Init the sensor as well. Allowed values: 0 disabled , 1(default) enabled */
#define GPS_ENABLED 1                       /* Enable Ublox GPS. Init the GPS as well. Allowed values: 0 disabled , 1(default) enabled */
#define RADIO_ENABLED 1                     /* Enable Radio. WARNING: DISABLED OPTION NOT TESTED PROPERLY. Allowed values: 0 disabled , 1(default) enabled */
#define USE_LED 1                           /* Enable LED blinky. Allowed values: 0 disabled , 1(default) enabled */
#define USE_NVM_STORED_LORAWAN_REGION 1     /* Use LoRaWAN region stored in EEPROm. Allowed values: 0 disabled , 1(default) enabled. If not using EEPROM location, \
#define SET_EU_RX1_DELAY_DEFAULT_5_SECOND 0 /* Set the EU868 RX1 delay to default of 5 seconds. Not LoRaWAN compliant, but default on TTN after it sends commands to \
#define GPS_LOCATION_FIX_TIMEOUT 180000
#define GPS_WAKEUP_TIMEOUT 1000
#define LORAWAN_APP_DATA_BUFF_SIZE 242
#define DOWNLINK_CONFIG_PORT 18
#define HOW_OFTEN_TO_SAVE_POS_TIM_TO_EEPROM 20U /* Save to eeprom every 20 minutes */
#define DEFAULT_N_POSITIONS_TO_SEND 13U         /* Number of past positions to send in each transmission */
#define MAX_N_POSITIONS_TO_SEND 25U
#define DEFAULT_N_POSITIONS_OFFSET 0U
#define PLAYBACK_DAYS 30U /* How many days ago to send playback positions(default). Max 45 days*/
#define USE_WATCHDOG 1 /* Use watchdog. Allowed values: 0 disabled , 1(default) enabled */
#define APP_TX_DUTYCYCLE 40000
#define LORAWAN_ADR_STATE LORAWAN_ADR_OFF
#define SAVE_FRAME_COUNTER_IN_INTERNAL_EEPROM 0 /* Storing frame counter in EEPROM. Allowed values: 0 disabled , 1 (default) enabled */

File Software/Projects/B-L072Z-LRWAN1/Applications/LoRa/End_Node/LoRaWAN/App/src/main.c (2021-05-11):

/**
  ******************************************************************************
  * @file    main.c
  * @author  MCD Application Team
  * @brief   this is the main!
  ******************************************************************************
  * @attention
  *
  * <h2><center>&copy; Copyright (c) 2018 STMicroelectronics.
  * All rights reserved.</center></h2>
  *
  * This software component is licensed by ST under Ultimate Liberty license
  * SLA0044, the "License"; You may not use this file except in compliance with
  * the License. You may obtain a copy of the License at:
  *                             www.st.com/SLA0044
  *
  ******************************************************************************
  */

/* Includes ------------------------------------------------------------------*/
#include "hw.h"
#include "low_power_manager.h"
#include "lora.h"
#include "bsp.h"
#include "timeServer.h"
#include "vcom.h"
#include "version.h"
#include "ublox.h"
#include "geofence.h"
#include "main.h"
#include "reset_debug.h"
#include "playback.h"


//#define LOW_POWER_DISABLE

// IMPT define switches in main.h to use or not use the GPS, sensor and radio and app duty cycle
#define LPP_APP_PORT 99

#define WATCHDOG_PAT_INTERVAL 10000 // milliseconds

/*!
 * LoRaWAN application port
 * @note do not use 224. It is reserved for certification
 */
#define LORAWAN_APP_PORT 2
/*!
 * LoRaWAN default endNode class port
 */
#define LORAWAN_DEFAULT_CLASS CLASS_A
/*!
 * LoRaWAN default confirm state
 */
#define LORAWAN_DEFAULT_CONFIRM_MSG_STATE LORAWAN_UNCONFIRMED_MSG

/*!
 * User application data
 */
static uint8_t AppDataBuff[LORAWAN_APP_DATA_BUFF_SIZE];

/*!
 * User application data structure
 */
//static lora_AppData_t AppData={ AppDataBuff,  0 ,0 };
lora_AppData_t AppData = {AppDataBuff, 0, 0};


/* call back when LoRa endNode has received a frame*/
static void LORA_RxData(lora_AppData_t *AppData);

/* call back when LoRa endNode has just joined*/
static void LORA_HasJoined(void);

/* call back when LoRa endNode has just switch the class*/
static void LORA_ConfirmClass(DeviceClass_t Class);

/* call back when server needs endNode to send a frame*/
static void LORA_TxNeeded(void);

/* LoRa endNode send request*/
static void Send(void *context);

/* start the tx process*/
static void LoraStartTx(TxEventType_t EventType);

/* tx timer callback function*/
static void OnTxTimerEvent(void *context);

/* tx timer callback function*/
static void LoraMacProcessNotify(void);

/* calculate datarate depending on region */
int8_t datarate_calculator(LoRaMacRegion_t LoRaMacRegion);

/* Watchdog pat functions */
static void OnWatchdogPatEvent(void *context);
void watchdog_pat_timer_init(void);

/* load Main call backs structure*/
static LoRaMainCallback_t LoRaMainCallbacks = {HW_GetBatteryLevel,
											   HW_GetTemperatureLevel,
											   HW_GetUniqueId,
											   HW_GetRandomSeed,
											   LORA_RxData,
											   LORA_HasJoined,
											   LORA_ConfirmClass,
											   LORA_TxNeeded,
											   LoraMacProcessNotify};
LoraFlagStatus LoraMacProcessRequest = LORA_RESET;
LoraFlagStatus AppProcessRequest = LORA_RESET;
LoraFlagStatus WatchdogPatRequest = LORA_RESET;

static TimerEvent_t TxTimer;
static TimerEvent_t WatchdogPatTimer;

// Set up brown out reset voltage as low as possible
void set_brownout_level(void);


/**
  * @brief  Main program
  * @param  None
  * @retval None
  */
int main(void)
{
	reset_cause_t reset_cause = reset_cause_get();

	/* STM32 HAL library initialization*/
	HAL_Init();

	/* Configure the system clock*/
	SystemClock_Config();

	/* Configure the debug mode*/
	DBG_Init();

	/* Set Brown out reset level voltage to 1.7V */
	set_brownout_level();

	/* Initialise serial debug interface */
	TraceInit();
	PRINTF("\n\nThe system reset cause is \"%s\"\n", reset_cause_get_name(reset_cause));

	PRINTF("\r\n\r\n");
	PRINTF("************************************ \r\n");
	PRINTF("* Picotracker Lora                 * \r\n");
	PRINTF("* Imperial College Space Society   * \r\n");
	PRINTF("************************************ \r\n\r\n");

	PRINTF("SELFTEST: Initialising Hardware\n\r");

	/* Configure the hardware*/
	HW_Init();

	HAL_IWDG_Refresh(&hiwdg);

	/*Disbale Stand-by mode*/
	LPM_SetOffMode(LPM_APPLI_Id, LPM_Disable);

	HAL_IWDG_Refresh(&hiwdg);

#if GPS_ENABLED
	/* GET intial location fix to set LORA region 
	 * The program cannot go on to unless it gets a GPS fix. It is neccessary for it to try forever
	 * It needs a GPS fix to get the right LoRa params for the region
	 */
	PRINTF("SELFTEST: Attempting to get a GPS fix\n\r");
	get_location_fix(GPS_LOCATION_FIX_TIMEOUT);

	HAL_IWDG_Refresh(&hiwdg);

	if (get_latest_gps_status() == GPS_SUCCESS)
	{
		/* Find out which region of world we are in and update region parm*/
		update_geofence_position(gps_info.GPS_UBX_latitude_Float, gps_info.GPS_UBX_longitude_Float);

		HAL_IWDG_Refresh(&hiwdg);

		/* Save current polygon to eeprom only if gps fix was valid */
		EepromMcuWriteBuffer(LORAMAC_REGION_EEPROM_ADDR, (void *)&current_geofence_status.current_loramac_region, sizeof(LoRaMacRegion_t));

		HAL_IWDG_Refresh(&hiwdg);
	}
	else
	{
/* read the eeprom value instead */
// TODO: must ensure that eeprom is not filled with garbage. i.e. when the eeprom has never been programed
#if USE_NVM_STORED_LORAWAN_REGION
		EepromMcuReadBuffer(LORAMAC_REGION_EEPROM_ADDR, (void *)&current_geofence_status.current_loramac_region, sizeof(LoRaMacRegion_t));
#endif

		HAL_IWDG_Refresh(&hiwdg);
	}

#endif

	PRINTF("SELFTEST: Now the radio should transmit\n\r");

	PRINTF("APP DUTY CYCLE(TX INTERVAL maybe longer depending on message length and datarate) : %d\n\r", APP_TX_DUTYCYCLE);

	while (1)
	{

		/* select data rate depending on region of the world. */
		int8_t dr = datarate_calculator(current_geofence_status.current_loramac_region);

		LoRaParam_t LoRaParamInit = {LORAWAN_ADR_STATE, dr, LORAWAN_PUBLIC_NETWORK};

		/* Configure the Lora Stack*/
		LORA_Init(&LoRaMainCallbacks, &LoRaParamInit); // sets up LoRa settings depending on the location we are in.

		HAL_IWDG_Refresh(&hiwdg);

		PRINTF("RANDTEST:%d\n", randr(1, 100));

/* Send a join request */
#if RADIO_ENABLED
		LORA_Join();

		HAL_IWDG_Refresh(&hiwdg);

		/* Init and start the tx interval timer */
		LoraStartTx(TX_ON_TIMER);

		HAL_IWDG_Refresh(&hiwdg);

#endif

		watchdog_pat_timer_init();

		/* Keep transmiting data packets every period defined by APP_TX_DUTYCYCLE */
		while (1)
		{

			if (AppProcessRequest == LORA_SET)
			{
				/*reset notification flag*/
				AppProcessRequest = LORA_RESET;

				/*Here lies the function to read sensor and GPS, parse and send it*/
				Send(NULL);
				/* if the tracker moves into another region, break out of main loop and 
				* reinit LoRa radio regional params
				*/
				if (current_geofence_status.lora_settings_status == INCORRECT)
				{

					PRINTF("Breaking out of main loop to reinit LoRa regional settings\n\r");
					TimerStop(&TxTimer);

					break;
				}
			}

			if (LoraMacProcessRequest == LORA_SET)
			{
				/*reset notification flag*/
				LoraMacProcessRequest = LORA_RESET;
				LoRaMacProcess();
			}

			if (WatchdogPatRequest == LORA_SET)
			{
				/*Pat the watchdog*/
				WatchdogPatRequest = LORA_RESET;
				HAL_IWDG_Refresh(&hiwdg);
			}

			/*If a flag is set at this point, mcu must not enter low power and must loop*/
			DISABLE_IRQ();

			/* if an interrupt has occurred after DISABLE_IRQ, it is kept pending 
			 * and cortex will not enter low power anyway  */
			if ((LoraMacProcessRequest != LORA_SET) && (AppProcessRequest != LORA_SET) && (WatchdogPatRequest != LORA_SET))
			{
#ifndef LOW_POWER_DISABLE
				LPM_EnterLowPower();
#endif
			}

			ENABLE_IRQ();

		}
	}
} // END main()

void LoraMacProcessNotify(void)
{
	LoraMacProcessRequest = LORA_SET;
}

static void LORA_HasJoined(void)
{
#if (OVER_THE_AIR_ACTIVATION != 0)
	PRINTF("JOINED\n\r");
#endif
	LORA_RequestClass(LORAWAN_DEFAULT_CLASS);
}

static void Send(void *context)
{
	HAL_IWDG_Refresh(&hiwdg);

	/* now join if not yet joined. */
#if RADIO_ENABLED
	if (LORA_JoinStatus() != LORA_SET)
	{
		/* Go ahead and join */
		LORA_Join();

		HAL_IWDG_Refresh(&hiwdg);

		return;
	}
#endif

	/* Temporarily stop tx interval timer until GPS gets a lock */
	// TODO: this timerstop MUST be removed.
	TimerStop(&TxTimer);

	HAL_IWDG_Refresh(&hiwdg);

	/* reading sensors and GPS */
	BSP_sensor_Read();

	/* Restart tx interval timer */
	TimerStart(&TxTimer);

	if (get_latest_gps_status() == GPS_SUCCESS)
	{
		/* Find out which region of world we are in and update region parm*/
		update_geofence_position(gps_info.GPS_UBX_latitude_Float, gps_info.GPS_UBX_longitude_Float);

		/* Save current polygon to eeprom only if gps fix was valid */
		EepromMcuWriteBuffer(LORAMAC_REGION_EEPROM_ADDR, (void *)&current_geofence_status.current_loramac_region, sizeof(LoRaMacRegion_t));

		HAL_IWDG_Refresh(&hiwdg);
	}

	/* reinit everything if it enters another LoRaWAN region. */
	if (current_geofence_status.lora_settings_status == INCORRECT)
	{
		PRINTF("LoRa Regional settings incorrect. Data send terminated\n\r");

		HAL_IWDG_Refresh(&hiwdg);

		return;
	}

	/* Don't tx when over regions where we are not supposed to tx
   * There is currenly no region defined in geofence.h that prohibits tx.
   */
	if (current_geofence_status.tx_permission == TX_NOT_OK)
	{
		TVL1(PRINTF("Entered NO tx region. Data send terminated\n\r");)

		HAL_IWDG_Refresh(&hiwdg);

		return;
	}

	prepare_tx_buffer();

	HAL_IWDG_Refresh(&hiwdg);

	AppData.Port = LPP_APP_PORT;
	AppData.Buff = get_tx_buffer();
	AppData.BuffSize = get_tx_buffer_len();

	// Print out buffer for debug
	PRINTF("Buffer to tx:\n");

	for (int i = 0; i < AppData.BuffSize; i++)
	{
		PRINTF("%02x", AppData.Buff[i]);
	}
	PRINTF("\n");
	PRINTF("tx_str_buffer_len: %d\n\n", AppData.BuffSize);

#if RADIO_ENABLED
	LORA_send(&AppData, LORAWAN_DEFAULT_CONFIRM_MSG_STATE);
#endif

	HAL_IWDG_Refresh(&hiwdg);
}

static void LORA_RxData(lora_AppData_t *AppData)
{
	/* USER CODE BEGIN 4 */
	PRINTF("PACKET RECEIVED ON PORT %d\n\r", AppData->Port);

	switch (AppData->Port)
	{
	case 3:
		/*this port switches the class*/
		if (AppData->BuffSize == 1)
		{
			switch (AppData->Buff[0])
			{
			case 0:
			{
				LORA_RequestClass(CLASS_A);
				break;
			}
			case 1:
			{
				LORA_RequestClass(CLASS_B);
				break;
			}
			case 2:
			{
				LORA_RequestClass(CLASS_C);
				break;
			}
			default:
				break;
			}
		}
		break;

	case LORAWAN_APP_PORT:
		break;

	case LPP_APP_PORT:
		break;

	case DOWNLINK_CONFIG_PORT:

		PRINTF("Received data: ");

		for (int i = 0; i < AppData->BuffSize; i++)
		{
			PRINTF("%02x", AppData->Buff[i]);
		}
		PRINTF("\n\n");

		manage_incoming_instruction(AppData->Buff);

		break;

	default:
		break;
	}
	/* USER CODE END 4 */
}

static void OnWatchdogPatEvent(void *context)
{
	TimerStart(&WatchdogPatTimer);
	WatchdogPatRequest = LORA_SET;
}

void watchdog_pat_timer_init()
{
	/* send everytime timer elapses */
	TimerInit(&WatchdogPatTimer, OnWatchdogPatEvent);
	TimerSetValue(&WatchdogPatTimer, WATCHDOG_PAT_INTERVAL);
	OnWatchdogPatEvent(NULL);
}

static void OnTxTimerEvent(void *context)
{
	/* Wait for next tx slot. 
	 * An interrupt service routine
	 * The timer, &TxTimer, calls this function after the elapsed time of length defined
	 * by APP_TX_DUTYCYCLE. Then this function tells the tracker that it is safe to transmit
	 * now by setting AppProcessRequest.
	 * This function also restarts the timer so that it can get called again after
	 * the elapsed period.
	 */
	TimerStart(&TxTimer);

	AppProcessRequest = LORA_SET;
}

static void LoraStartTx(TxEventType_t EventType)
{
	if (EventType == TX_ON_TIMER)
	{
		/* send everytime timer elapses */
		TimerInit(&TxTimer, OnTxTimerEvent);
		TimerSetValue(&TxTimer, APP_TX_DUTYCYCLE);
		OnTxTimerEvent(NULL);
	}
	else
	{
		/* send everytime button is pushed */
		GPIO_InitTypeDef initStruct = {0};

		initStruct.Mode = GPIO_MODE_IT_RISING;
		initStruct.Pull = GPIO_PULLUP;
		initStruct.Speed = GPIO_SPEED_HIGH;

		HW_GPIO_Init(USER_BUTTON_GPIO_PORT, USER_BUTTON_PIN, &initStruct);
		HW_GPIO_SetIrq(USER_BUTTON_GPIO_PORT, USER_BUTTON_PIN, 0, Send);
	}
}

static void LORA_ConfirmClass(DeviceClass_t Class)
{
	PRINTF("switch to class %c done\n\r", "ABC"[Class]);

	/*Optionnal*/
	/*informs the server that switch has occurred ASAP*/
	AppData.BuffSize = 0;
	AppData.Port = LORAWAN_APP_PORT;

	LORA_send(&AppData, LORAWAN_UNCONFIRMED_MSG);
}

static void LORA_TxNeeded(void)
{
	AppData.BuffSize = 0;
	AppData.Port = LORAWAN_APP_PORT;

	LORA_send(&AppData, LORAWAN_UNCONFIRMED_MSG);
}

void set_brownout_level(void)
{ /*  BOR Reset threshold levels for 1.7V - 1.8V VDD power supply */
	if ((FLASH_OB_GetBOR() & 0x0F) != OB_BOR_LEVEL1)
	{
		HAL_FLASH_Unlock();
		/* Unlocks the option bytes block access */
		HAL_FLASH_OB_Unlock();
		/* Clears the FLASH pending flags */
		__HAL_FLASH_CLEAR_FLAG(FLASH_FLAG_EOP | FLASH_FLAG_WRPERR |
							   FLASH_FLAG_PGAERR | FLASH_FLAG_SIZERR | FLASH_FLAG_OPTVERR);
		/* Select The Desired V(BOR) Level------------------------*/
		FLASH_OB_BORConfig(OB_BOR_LEVEL1);
		/* Launch the option byte loading and generate a System Reset */
		HAL_FLASH_OB_Launch();

		HAL_FLASH_Lock();
	}
}

/**
* Use datarate of DR_5 over the EU but DR_4 over rest of the world
*/
int8_t datarate_calculator(LoRaMacRegion_t LoRaMacRegion)
{
	int8_t dr = 0;

	switch (LoRaMacRegion)
	{
	case LORAMAC_REGION_EU868:
		dr = DR_5;
		break;

	default:
		dr = DR_4;
		break;
	}

	return dr;
}

/************************ (C) COPYRIGHT STMicroelectronics *****END OF FILE****/

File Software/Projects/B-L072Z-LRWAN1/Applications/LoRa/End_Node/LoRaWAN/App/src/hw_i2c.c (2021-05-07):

/**
  ******************************************************************************
  * File Name          : I2C.c
  * Description        : This file provides code for the configuration
  *                      of the I2C instances.
  ******************************************************************************
  * @attention
  *
  * <h2><center>&copy; Copyright (c) 2020 STMicroelectronics.
  * All rights reserved.</center></h2>
  *
  * This software component is licensed by ST under BSD 3-Clause license,
  * the "License"; You may not use this file except in compliance with the
  * License. You may obtain a copy of the License at:
  *                        opensource.org/licenses/BSD-3-Clause
  *
  ******************************************************************************
  */

/* Includes ------------------------------------------------------------------*/
#include "hw_i2c.h"
#include "debug.h"

I2C_HandleTypeDef hi2c1;

/* I2C1 init function */
void MX_I2C1_Init(void)
{

  hi2c1.Instance = I2C1;
  hi2c1.Init.Timing = 0x00707CBB;
  hi2c1.Init.OwnAddress1 = 0;
  hi2c1.Init.AddressingMode = I2C_ADDRESSINGMODE_7BIT;
  hi2c1.Init.DualAddressMode = I2C_DUALADDRESS_DISABLE;
  hi2c1.Init.OwnAddress2 = 0;
  hi2c1.Init.OwnAddress2Masks = I2C_OA2_NOMASK;
  hi2c1.Init.GeneralCallMode = I2C_GENERALCALL_DISABLE;
  hi2c1.Init.NoStretchMode = I2C_NOSTRETCH_DISABLE;
  if (HAL_I2C_Init(&hi2c1) != HAL_OK)
  {
    Error_Handler();
  }

}

void HAL_I2C_MspInit(I2C_HandleTypeDef* i2cHandle)
{

  GPIO_InitTypeDef GPIO_InitStruct = {0};
  if(i2cHandle->Instance==I2C1)
  {
  
    __HAL_RCC_GPIOB_CLK_ENABLE();
    /**I2C1 GPIO Configuration    
    PB9     ------> I2C1_SDA
    PB8     ------> I2C1_SCL 
    */
    GPIO_InitStruct.Pin = GPIO_PIN_9|GPIO_PIN_8;
    GPIO_InitStruct.Mode = GPIO_MODE_AF_OD;
    GPIO_InitStruct.Pull = GPIO_PULLUP;
    GPIO_InitStruct.Speed = GPIO_SPEED_FREQ_VERY_HIGH;
    GPIO_InitStruct.Alternate = GPIO_AF4_I2C1;
    HAL_GPIO_Init(GPIOB, &GPIO_InitStruct);

    /* I2C1 clock enable */
    __HAL_RCC_I2C1_CLK_ENABLE();
		
		/* I2C1 interrupt Init */
    HAL_NVIC_SetPriority(I2C1_IRQn, 0, 0);
    HAL_NVIC_EnableIRQ(I2C1_IRQn);
  }
}

void HAL_I2C_MspDeInit(I2C_HandleTypeDef* i2cHandle)
{

  if(i2cHandle->Instance==I2C1)
  {
    /* Peripheral clock disable */
    __HAL_RCC_I2C1_CLK_DISABLE();
  
    /**I2C1 GPIO Configuration    
    PB9     ------> I2C1_SDA
    PB8     ------> I2C1_SCL 
    */
    HAL_GPIO_DeInit(GPIOB, GPIO_PIN_9|GPIO_PIN_8);
		
		/* I2C1 interrupt Deinit */
    HAL_NVIC_DisableIRQ(I2C1_IRQn);

  }
} 

/************************ (C) COPYRIGHT STMicroelectronics *****END OF FILE****/

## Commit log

2019-10-18 removed the picotracker mk II software files
    [ICSSPicoTracker2.kicad_pcb, ICSSPicoTracker2.sch, ICSSPicoTrackerGPS.sch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]
2019-10-19 added old files from project mach one flight computer
    [GPS.sch, MCU.sch, circuit board design.kicad_pcb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]
2019-10-19 removed the samd21 and put in the murata
    [GPS.sch, MCU.sch, circuit board design.sch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]
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2019-10-19 setup power connections to mcu
    [MCU.sch]
2019-10-19 set up antenna pi network
    [MCU.sch]
2019-10-21 Moved all schematic parts to a single sheet
    [GPS.sch, MCU.sch, circuit board design.sch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]
2019-10-21 removed the hierachial files
    [GPS.sch, MCU.sch, power_supply.sch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]
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2019-10-22 Add other parts to repository
    [Xplained_RFM98W.sch, circuit board design.kicad_pcb, circuit board design.sch]
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2019-10-24 made some edits to the circuit to remove ERC errors. Added in footprints from Femto
    [circuit board design.kicad_pcb, circuit board design.sch]
2019-10-24 moved txco power to PB15
    [circuit board design.sch]
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2019-10-24 changed the footprints for GPS antenna and lora antenna
    [circuit board design.kicad_pcb, circuit board design.sch]
2019-10-24 put in solar voltage adc measurments
    [circuit board design.sch]
2019-10-24 Fully routed the board
    [circuit board design.kicad_pcb, circuit board design.sch]
2019-10-25 Changed the TCXO power pin. Changed the track width for RF transmission lines to 0.86mm
    [circuit board design.kicad_pcb, circuit board design.sch]
2019-10-26 added in indicator LED, added in push button to circuit only.
    [circuit board design.kicad_pcb, circuit board design.sch, locations of gateways that picked up our transmissions on 26-10-19.csv]
2019-10-29 added the switch. reorganised the prototype folder to have a "a" variant
    [circuit board design.kicad_pcb, circuit board design.sch]
2019-10-29 finished the layout of the simple version a
    [circuit board design.sch]
2019-10-29 Finished the design for the batteryless version
    [circuit board design.kicad_pcb]
2019-10-29 made a copy for a battery powered version
    [circuit board design.kicad_pcb, circuit board design.sch]
2019-10-29 added in the libraries to the b variant from femto
    [circuit board design.sch]
2019-10-29 updated the "b" variant
    [circuit board design.kicad_pcb, circuit board design.sch, pecanfemto5.sch]
2019-10-29 mostly wired up the "b" variant. Changed the fill clearance for copper pour for the "a" variant to a much smaller 0.15mm
    [circuit board design.kicad_pcb, circuit board design.sch]
2019-10-30 changed the layout of schematic of "b" variant to save space
    [circuit board design.sch]
2019-10-31 updated circuit of b variant for low power voltage measurment. Made a variant tcxo enable controllable
    [circuit board design.kicad_pcb, circuit board design.sch, transfer.sch]
2019-10-31 Power GPS through SENSE_VCC
    [circuit board design.sch]
2019-10-31 Connected ABZ output pin to GPS back up pin for b variant
    [circuit board design.sch]
2019-11-01 Routed most of the b variant of the board
    [circuit board design.kicad_pcb, circuit board design.sch]
2019-11-01 Finished the routing of the b variant.
    [circuit board design.kicad_pcb]
2019-11-01 Routed most of the swaped config board
    [circuit board design.kicad_pcb, circuit board design.sch]
2019-11-01 rerouted the "a" variant to place the RF output pin of abz module closer to antenna
    [circuit board design.kicad_pcb, circuit board design.sch]
2019-11-02 Finished the layout of both the a and b variants. Silkscreen also done
    [circuit board design.kicad_pcb, circuit board design.sch]
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2019-11-05 updated the bom with links to purchase. got the interactive bom to work
    [circuit board design.kicad_pcb, circuit board design.sch]
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2019-11-27 did some test code and made the v1.1 for a and b variants
    [circuit board design.kicad_pcb, circuit board design.sch, pecanfemto5.sch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]
2019-11-27 finished lora tracker v1.1 for a and b variants
    [circuit board design.kicad_pcb, circuit board design.sch]
2019-11-30 put in the ST example code for their STEVAL-STRKT01, modified for lora tracker
    [GetGNSSConfigurationData.txt, GetLoRaJoinParameters.txt, LoRa_STEVAL_STRKT01 Debug.cfg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]
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2019-12-19 filter out 0xff data but still errors are present
    [main.c, main.h]
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2019-12-28 put in gps coordinates for geofencing.
    but it is not fully working. theere are quite a few false positives. a point is being identified as being part of other polygons.
    [coordinates problem australia.csv]
2019-12-28 re activiated gps fix section
    [main.c]
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2019-12-28 added back gps passthrough project folder by Richard, got rid of my early pico tracker lora project folder that does not work
    [main.c, main.h]
2019-12-28 changed the programmer to st link. included a reset default config for gps, both for the GPS passthrough project
    [main.c]
2019-12-28 tracker can now get a fix and save to variables
    [main.c]
2019-12-28 GPS works, it responds and sends back coordinates. but gps sleep is not working well. it is not waking up and getting a fix quickly
    [main.c]
2019-12-28 currently testing geofence. revert commit to use gps
    [main.c]
2019-12-30 refactored gps fix type, added the powersave config and command
    [main.c]
2019-12-30 refactored gps fix status variables. added in pm2 config message
    [main.c]
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2020-01-13 moved main project software closer to project root to make path lengths shorter
    [bsp.c, bsp.h, debug.c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]
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2020-01-14 added in missing CAYENNE prefixes for GPS coordinates. updated variables to form cayenne strings for long,lat,alt.
    I think the type conversion should be correct. both use int32 represesntation for long,lat,alt
    [main.c]
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2020-01-17 GPS integration works a bit. Conversion to cayenn is not right.
    Need to get a clear view of sky to get GPS fix
    [bsp.c, main.c]
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2020-01-24 Just wanted to make sure that there is no chance of having an index error with printing two different sized channel mask arrays
    One for AU915 and one for the rest.
2020-01-24 fixed problem with backup pin not working. but power consumption is still high
    [main.c]
2020-01-25 in ublox.c, wrapped led blink indicators in an if statement to avoid blinking after launch
    [main.c]
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2020-01-31 put in brown out level of 2.8v for mcu, above gps
    [main.c, main.h]
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2020-02-05 put in the gnd hole for gnd plane. put in lots of vias
    [circuit board design.sch]
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2020-02-06 connected pin 1 to pin 8 on SPV1040
    [circuit board design.sch]
2020-02-06 connected pin 1 to pin 8 on spv1040 on the PCB
    [circuit board design.kicad_pcb]
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2020-03-11 put back latch to init timer
    CURRENTLY CODE IS BROKEN
    [main.c]
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2020-03-13 Fixed problem where tx interval timer triggers off while searching for GPS
    I temporarily stop the tx interval timer while it searches for a GPS fix
    [main.c]
2020-03-13 set brown out reset for MCU back to 1.7V.
    I think it is better to keep the MCU alive, than to keep it dead until the GPS fully wakes up
    [main.c]
2020-03-16 fixed bug with brown out level not correctly set
    [main.c]
2020-03-16 updated geofencing util programs
    cleaned up geofence util files
    updated util files to generate more verbose polygon data
    [coordinates problem australia.csv, country-capitals.csv, selected_country_capitals.csv]
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2020-03-19 successfully got the plan b working
    using gateway data only, I manage to localise the balloon
    [coords.csv, flight_payload_time.csv]
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2020-03-21 Made MCU wait until GPS threshold voltage is reached.
    Made it a priority for GPS to get a fix before starting to do anything else(e.g. send Radio join requests). I have set the GPS to search for a fix FOREVER and cannot do anything until it gets a fix. Realistically, if we don't know where we are, we won't know what LoRa params to set.
    [main.c, main.h]
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2020-03-25 Rever reset the frame counter. always continue.
    Frame counter is saved to EEPROM
    [bsp.c, bsp.h, main.c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]
2020-03-25 Revert "updated comments in main.h"
    This reverts commit d8cb793cb1b56b5174bf89aa0a6c7d0f16541ab5.
    [main.h]
2020-03-27 In this commit, frame counter is saved to EEPROM Which means that everytime the device is power cycled, it will continue from the previous Frame counter value. Authentication is switch by default to 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
    Cleaned up main.h
    [bsp.c, bsp.h, main.c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]
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2020-04-27 Fixed bug with I2C line locking up
    - I have used the I2C HAL implementation using interrupts instead of polling by changing from HAL_I2C_Master_Receive to HAL_I2C_Master_Receive_IT. Same for HAL_I2C_Master_Transmit to HAL_I2C_Master_Transmit_IT.
    - Used the implementation from the demo projects for the STM32L0
    - It appears that the I2C line locks up intermittently(anywhere after 1min to 30min after start).
    - The issue does not appear when using the default systick implementation using the crystal. However, when using the RTC to return systick values, it seems to somehow lock up the I2C line after a while. I suspect it may be causing a Race condition somewhere. Maybe with interrupts.
    [hw_i2c.c, main.c, main.h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]
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2020-05-29 removed the power voltage detector
    It is not necessary. Just get a gps fix when the voltage reaches the target voltage but otherwise just send radio transmissions
    [main.c]
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2020-06-23 fixed printouts
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2020-07-07 finally used the same structure as orignial ublox code. but it resets every time!
    [main.h]
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2020-07-10 improve printout of gps fix info
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2020-08-21 don't call error handler when reinit i2c
    [i2c_middleware.c]
2020-08-21 reinit gps/i2c only when it does not get a fix
2020-08-21 let gps to search for a fix for 180 seconds, instead of 120 seconds
    [main.h]
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2020-08-25 Revert "reinit gps/i2c only when it does not get a fix"
    This reverts commit 337f41a8d6c632ac599359e3187cac0c6d100555.
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2020-08-27 read scl sda pin to check if stuck low before reset
    [i2c_middleware.c]
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2020-08-27 fix printouts
2020-08-27 do not reset if sda is stuck low
    [i2c_middleware.c]
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2020-09-01 Revert "Do printout nema from GPS if it comes through"
    This reverts commit 6441bf7145dea3dfca4785e70d0ef496b9007460.
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2020-09-02 Send two solar voltages: under load and under almost no load (#14)
    * refactor BSP_GetBatteryLevel16 to BSP_GetSolarLevel16
    * refactor battery_level16 to no_load_solar_voltage
    * put in new sensor value: load_solar_voltage
    * put in function to get solar voltage under load
    * refactor cayenne_battery_voltage to cayenne_no_load_voltage
    * put in cayenne_load_voltage
    * send 8 bit value to represent solar voltage.
    e.g. 3300mV is sent as 33 which will fit within a single byte.
    * fix cayenne output
    * dont unnecessarily cast
    [bsp.c, bsp.h, main.c]
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2020-10-22 fix missing number in print statement
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2020-11-06 Makeing board 1.3a (#30)
    * pull gps ddc and uart pins out to side test points
    * connect stm32 reset line to vcc via resistor
    * connect stm32 to gps via usart2
    * put in the test points
    * put in test point to switched gps power supply
    * update annotation
    * put test point name labels
    * put in solder jumper for uart. Connected i2c as well
    * changed the lora antenna pad to rectangular
    * made seperate custom abz foot print
    * made seperate folder for 1.3a design
    * put in pdf schematic of 1.3a
    [circuit board design.kicad_pcb, circuit board design.sch]
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2020-11-17 fix error in configuring uart for B_L072Z_LRWAN1
    [mlm32l0xx_hw_conf.h]
2020-11-17 Revert "disable sensors for this test. Only need radio"
    This reverts commit a3db65fedb6f0e13d16317d0e3b9d0d62024e044.
    [main.h]
2020-11-17 use correct method of overriding default power
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2020-11-23 fix issue where frame counter was not loading properly from EEPROM
2020-11-23 Revert "use LSI crystal instead of LSE"
    This reverts commit 10a8ec7da5778086a306b6f2c7c6a77101f1cc74.
    [mlm32l0xx_hal_msp.c]
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2020-12-25 save position to eeprom with every fix; (#45)
    increment count only after 20 minutes
    [bsp.c]
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2021-01-09 Print reset cause (#55)
    * put in reset debug checker
    * move reset debug files
    * add reset debug files to project
    * put in reset case in the main.c
    * catch all reset causes
    * ban power saving configs for ublox
    * set gps fix timeout to 12 seconds
    * set reset cause check at the beginning
    * Revert "ban power saving configs for ublox"
    This reverts commit e9ef4cc4fa53b191b3ca5478ab9719000b76512d.
    * formating only
    [main.c]
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2021-01-09 dont go into low power mode so that the watchdog can be reset every loop
    [main.c]
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2021-01-09 #52 make it select positions from past n days (#54)
    * return only when a LGC result is found
    * define how long ago to select data from
    * intialise playback with number of positions to select from
    This allows the LGC to select from the last 10 days
    * update comment
    * update comment
    * refactor minute_from_epoch_to_time_pos_index() to get_time_pos_index_older_than()
    * correctly select earliest timepos_index
    * refactor n_positions_to_select_from to position_pool_size_to_select_from
    * update comment
    * get earliest timepos index in more readable way
    * use hardcoded lower value of 0
    * just select from pool size
    * update comment
    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
    [bsp.c, bsp.h, main.h]
2021-01-11 Ensure counter increments (#65)
    * make seperate function to increment eeprom indexes
    * puti n seperate function to playback_hw_init()
    * put in seperate function to update reset counts
    * do iwdg refresh whenever reading from EEPROM
    * add function to pretty print sensor values
    * put seperate function to save data to nvm
    * update documentation
    * put in function to fill structs to send to gnd
    * formatting and adding comments
    * print normally
    * [needs improvement] put in workaround to increment index counter
    In the very first transmission, it skips writing to the first index. Then later, the program reads this first index, all 0s, and gets conf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
    [bsp.c, main.h, mlm32l0xx_hw.c]
2021-01-11 Revert "Update main.h"
    This reverts commit 0898c2070c029d1b4721674434a0c6dc658d41c4.
    [main.h]
2021-01-15 Clean up repo (#68)
    * remove unused parts of repo
    * move util scripts
    * put back csv files that got gitignored
    * allow back csv and xml files to be version controlled
    It is too broad,
    * put back pycharm files
    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
    [HAB2Bb.STL, HabB2a.STL, LoRa Jig Bottom.stl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]
2021-04-20 Fixes issue #67 (#72)
    * pat watchdog every 10 seconds
    Don't pat it every loop around the main loop
    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
    [main.c]
2021-04-20 skip bsp read on the first gps read
    Because it is already read to set geofence.
    [main.c]
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2021-04-20 get internal temperature if not using ms5607
    Fixes #78
    [bsp.c]
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2021-04-20 remove all the pointless toggling of the power to gps (#23)
    * remove all the pointless toggling of the power to gps
    Also remove toggling of scl and sda lines
    * remove uncessary function
    * put in i2c error debug message
    * remove all the pointless toggling of the power to gps
    Also remove toggling of scl and sda lines
    * remove uncessary function
    * put in i2c error debug message
    * never factory reset the gps.
    * remove commented out text
    * remove unused functions for i2c pins
    * Auto format only
    * remove unused comments ONLY
    * Revert "remove unused comments ONLY"
    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
    [i2c_middleware.c]
2021-04-20 Disable sensor by default.
    It is no longer flying due to running out of sensors. Use internal thermistor for temperature reading. No pressure reading.
    [main.h]
2021-04-20 Undo gps speedups (#79)
    * Revert "allow gps setup time"
    This reverts commit 9c3a234cf366b20f990b061b9f6b56ca71cf5779.
    * Revert "remove all the pointless toggling of the power to gps (#23)"
    This reverts commit eed6288b24fdbbf9db9de31db993c0a207acc879.
    [i2c_middleware.c]
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2021-04-27 don't read gps 2 times after boot
    Fixes issue where the string to send down was not being created on the first transmission
    [main.c]
2021-04-28 Revert "Merge pull request #82 from ImperialSpaceSociety/ensure-it-does-not-send-rubbish-on-first-tx-after-boot"
    This reverts commit e195ceaba68dc01ac17e0bdb45b6abec64d9d036, reversing
    changes made to c496bae3c0ef7b593c40b80a990ebcef2f49b612.
    [bsp.c, bsp.h, main.c]
2021-04-28 Revert "skip bsp read on the first gps read"
    This reverts commit b49410338984fa66606cb7592720f4883dbe9c04.
    [main.c]
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2021-05-06 fix compile error where Error_handler() function was not found.
    Import the header file for it.
    [hw_i2c.c]
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2021-05-11 fix bug in getting current_loramac_region
    [main.c]
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2021-07-09 Fix pointless uplinks after boot on TTNv3
    Disable SetMlmeScheduleUplinkIndication(...).
    This uplink is sent until a downlink is sent from server to ack that settings have been successful. However, the TTN server does not send this downlink, and the tracker ends up sending these uplinks forever. So just disable them.
    don't save fcount to eeprom
    Restart from zero after each reset, to ensure the server sends up the RX1 delay window settings and channel selection each time.
    don't set rx1 day to 5s by default
    Get the server to send the settings each time
    [main.h]
2021-07-09 Revert "switch to uart speed of 115200 baud"
    This reverts commit bc279e9b7986a5bafe161c714f75fffb3111a8b5.
    [vcom.c]

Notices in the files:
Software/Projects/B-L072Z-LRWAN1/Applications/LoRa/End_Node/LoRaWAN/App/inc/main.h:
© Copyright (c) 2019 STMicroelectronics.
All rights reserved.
